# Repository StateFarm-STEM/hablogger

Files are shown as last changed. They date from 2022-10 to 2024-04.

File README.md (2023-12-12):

# High altitude Balloon (HAB) Logger

HABLogger is a project built to be usable by schools, community groups, youth organizations, and more as an introduction to programming, electronics and team building.

The [National Weather Service](https://www.weather.gov/chs/upperair) launches a minimum of two high altitude balloons a day from [91 locations](https://www.weather.gov/upperair/nws_upper) at 1100 and 2300 UTC to observe weather conditions used to model weather forecasts. When flying high altitude ballons, data is usually collected throughout the flight and later retrieved for analysis.

This project contains lessons wherein learners will launch their own weather balloon to the stratosphere, or approximately 90,000+ feet. Throughout the balloon flight, the components within the payload will collect temperature, barometric pressure, latitude, longitude, elevation, and other telemetry data. This information is collected via the peripheral modules attached to the microcontrollers within the payload and stored in an SD card for analysis after recovery.

The project contains basic hands-on experiences with the following:

- Microcontrollers & electronics, including wiring peripheral modules between a microcontroller and breadboard
- Programming microcontrollers to interact with peripheral modules using C programming language (Arduino microcontroller) or Python (Raspberry Pi Pico microcontroller)
- Launching a finished product in a high-altitude balloon flight to the stratosphere (90,000+ feet)
- Analyzing collected data after recovering the balloon payload

Each lesson is constructed to be completed within the timeframe of a typical classroom experience (approximately 45 minutes to 1 hour), and are designed to be completed by small groups (between 2 and 5 learners is recommended)

## Lesson Overview

- Lesson 1: Introduction and how to get started
  - Details about high altitude balloons
  - Introduction to electronics and components used in the project
  - Installing and using the preferred integrated development enviornment (IDE)
- Lesson 2: Blinking lights
  - Traditional first project with microcontrollers getting students comfortable with breadboards, components, microcontrollers, and loading code to the device 
- Lesson 3: Working with the weather sensor
  - Wiring up sensors to read temperature and barometric pressure
- Lesson 4: Working with the GPS module
  - Wiring up GPS hardware to the microcontroller and reading satellite telemetry
- Lesson 5: Working with the SD card module
  - Wire up SD card hardware then writing and reading contents from the SD card
- Lesson 6: Putting it all together
  - Wire everything up and write telemetry data to SD card
  - Read telemetry data from the SD card
- Analyzing telemetry and log data
  - Samples to interpret flight data

### Accessing the Lessons

The content is divided up by language and within the language you can choose the platform (where applicable).
- [C](https://github.com/StateFarm-STEM/hablogger/tree/main/c)
- [Python](https://github.com/StateFarm-STEM/hablogger/tree/main/python)

# Need Help?

- Report an issue by clicking the [issue](https://github.com/StateFarm-STEM/hablogger/issues) link towards the top of the page

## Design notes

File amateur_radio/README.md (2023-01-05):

# Amateur Radio In This Project

## Goals
To track the High Altitude Balloon, Amateur Radio is leveraged.  There are other tracking options that do not require a license, but among the goals are:
 - Introduce Amateur Radio to students and educators
 - Introduce new types of wireless communication with hands-on learning
 - Demonstrate the benefits of Amateur Radio beyond the balloon project, such as being able to communicate during emergencies
 - Show students there are Amateur Radio scholarships available, if they obtain their license.

## Overview
Amateur Radio, also known as Ham Radio, is the use of radio communications for the purposes of non-commercial exchange of messages, wireless experimentation, self-training, private recreation, and emergency communications.

Amateur Radio is utilized by the project to track and collect real-time flight telemetry information from the High Altitude Balloon, and locating the payload after landing.  HAB tracking via Amateur Radio is performed commonly via two means:
- Automatic Packet Reporting System (APRS)
- Weak Signal Propagation Reporter (WSPR) (pronounced whisper)

Each option has benefits and limitations, depending on the types of balloon and the tracking goals.

## Automatic Packet Reporting System (APRS)

APRS is a real time digital communication system that allows participants to share information, including position infromation, and other information about their locale that has 'immediate value' to all participants.

In its widest implementation, APRS communication occurs using VHF radios, with messages relayed to other stations, including repeaters on the ground, which can deliver the locale and telemetry infromation to APRS internet sites that allow users to view a map of APRS objects.

APRS works well for tracking goals of:
- High accuracy tracking is required (such as for payload retrival)
- Expected flight path is within local or regional area
- Expected flight path does NOT cross ocean or international waters
- Expected flight of balloon is rise to a max altitude and immediately return to earth
- Expected flight duration is a few hours or days

## Weak Signal Propagation Reporter (WSPR)

WSPR (prounced "whisper") is a protocol designed for weak-signal radio communication.  It is commonly used to by amateur radio operators for sending and recieving very low-power transmissions to test propagatino path on the Medium Frequency (MF) and High Frequency (HF) bands.  The protocol is designed and written initially by Joe Taylor (K1JT) and uses open source software developed and supported by  small team.  WSPR transmission, similiar to APRS, use a standard message format, carrying the station's call sign, Madienhead grid locator, and transmitter power in dBm.  The program decodes signals with a signal-to-noise (SNR) as low as -28 dB, with stations sending reports to online central database called WSPRnet, which includes mapping.

### References

[Weak Signal Propagation Reporter (WSPR)](https://en.wikipedia.org/wiki/WSPR_(amateur_radio_software))
[WSPR - Distant Whispers](http://www.g4ilo.com/wspr.html)
[WSPRNet](http://www.wsprnet.org/drupal/wsprnet/map)

## Tracking the balloon

## Getting your licensce

[Ham Radio School](https://www.hamradioschool.com/)

## Helpful links

[APRS.org](http://www.aprs.org/)

## Citation

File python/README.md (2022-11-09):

# HAB Logger
High Altitude Balloon Data Logging Project

Currently the Python version is supported on [Raspberry Pico hardware](https://www.raspberrypi.com/products/raspberry-pi-pico/). Your welcome to test on other RP2040 hardware platforms. If you do please let us know about your work by opening an [issue](https://github.com/StateFarm-STEM/hablogger/issues)!

Access the lessons [here](https://github.com/StateFarm-STEM/hablogger/tree/main/python/raspberrypico)

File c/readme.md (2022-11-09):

# C Language versions of the HAB Logger

Currently the HAB Logger is available and ready for use on [Arduino hardware](https://github.com/StateFarm-STEM/hablogger/tree/main/c/arduino). 

We are working on porting to the Raspberry Pico, we appreciate your patience!

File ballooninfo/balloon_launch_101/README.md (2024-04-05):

# How To Launch a High Altitude BAlloon (HAB) For Carrying The Project

## Overview

## Prediction Details

### Burst Calculations

[SondeHub Burst Calculation Website](https://sondehub.org/calc/)

- Modify the fields with a red star for your needs:
  - Payload Mass is the weight of everything below the balloon you will be flying in grams. A simple [Google search](https://www.google.com/search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) will yield the conversions
    - Rigging line(s), parachute, payload harness, Payload nd contents, and anything attached to the payload
  - Ballon Mass is the size balloon you will be flying. Be sure to select the proper size AND manufacturer. It's not a bad idea to validate the specs as we found the burst diameter a bit off.
  - Target Ascent rate in meters per second
    - For best camera results an ascent of 6 meters per second is optimal but you will likely need a different rate based on your lift gas volume
      - A flow gauge can be used to dial in the right amount of gas but they are typically cost prohibitive. These gauges are typically different for each type of gas as well.
    - You will need to modify this until the volume changes to your lift gas tank volume. A simple [Google search](https://www.google.com/search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) can convert m3 to cubic feet
   - Gas needs to be changed ot the lift gas you will be using. The calculations will be different for each lift gas option!

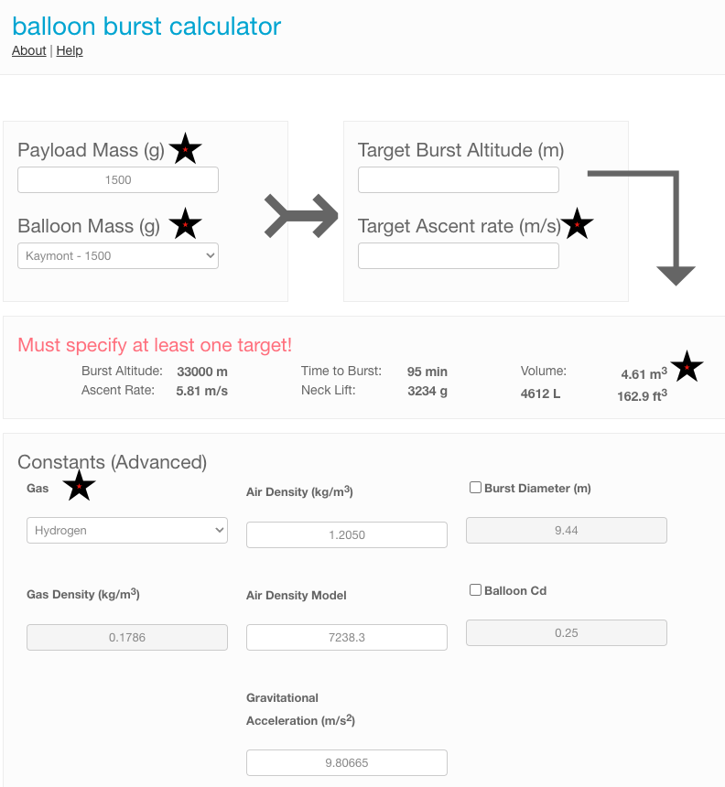
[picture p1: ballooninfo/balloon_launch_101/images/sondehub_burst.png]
SonceHub_Burst_image


## Landing Prediction Calculator

[Sonde HAB Prediction Calculator](https://predict.sondehub.org/)

- Modify the fields with a red star for your needs:
  - Latitude and Longitude
    - You can use many tools like [maps.google.com](maps.google.com)
      - Find the location best suited for winds at launch time and place a waypoint. The latitude and longitude will be shown or copied easily from the shared link
  - Launch Altitude
    - THis can be determined with many tools like Google Earth, USGS, [websites](https://whatismyelevation.com/), etc
      - Be sure to convert to meters
  - Launch time UTC
    - [Convert](https://www.google.com/search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) local time to UTC
- Launch Date
- Ascent Rate (m)
  - This was claculated fromt he above instructions on [SondeHub Burst Calculation Website](https://sondehub.org/calc/)
- Burst/Float Altitude (m)
  - This was claculated fromt he above instructions on [SondeHub Burst Calculation Website](https://sondehub.org/calc/)
- Descent Rate (m/s)
  - this will be defined by your parachute. Be sure you calculate based on the adjustments on your actual parachute as many can be reduced

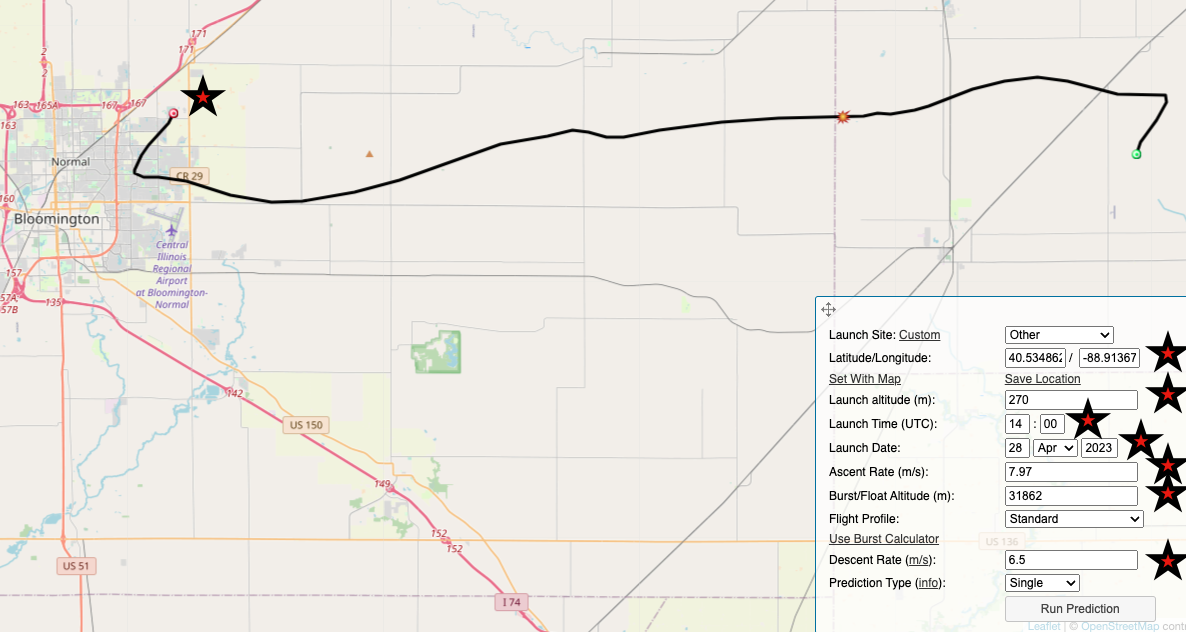
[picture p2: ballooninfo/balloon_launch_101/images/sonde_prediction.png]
SonceHub_Burst_image

-------

## Build payloads

### Pre-work / pre-launch

- Add camera mounts in the payload (top and sides)
- Mount external temp sensor and route wires to the logger
- Mount VHF antennas / dowell rods
  - Moxon
  - Di-pole
Ready the tracker(s)
- VHF APRS
- HF WSPR
- Other?
- Load batteries in the battery holders for the tracker
- Attach antennas to tracker(s) (HF and VHF)
Charge large battery packs
Data logger plugs into main battery pack

Ready Cameras
- Validate settings
- Ensure SD card is wiped
- Ensure they record a test video
  
Make rigging lines for filling and safety
- Two tethers for filling and moving to flight pad
- Rigging for payload attachment
- Release loop

Load everything needed for launch
- Battery
- Student data loggers(s)
- Tracker(s)
  - Battery pack(s)

Action Camera(s)
- Battery(s)
- SD card
Insta360
- Connect to battery(s) pack
- SD card(s)

Power splitter
If found contact note
Weather check / go no go
Prediciton calculation / go no go
Validate location of launch based on wind prediciton and / or other hazards
Contact local airport FAA / tower

### Day of launch

Weather check / go no go
Prediciton calculation / go no go
Setup filling station
- Stake tarp
- Unload tanks
- Ground tank
- Setup filler
  - Ground stake in the dirt
  - Ground wire attached to filler
- Setup rigging lines w caribeaners and attach:
  - To tank
  - To dumbell(s)
Undo balloon bag rubberbands

### Setup launch pads
Attach line to weight
Ensure team has their task list
Layout payload
- Layout payload downwind
- Kiteline to parachute
- Attach rigging line to parachute
- Rigging line to payload harness
- Attach 360 cam
- Attach rigging harness to payload

Power on battery pack(s)
Power on tracker
- Ensure pings are working on APRS and WSPR

Power on student data logger
Ensure all items are secure (duct tape where needed)
Setup cameras
- Plug into power
- Secure in camera holders
- Power insta360

Run prediction and share content / go no go
Monitor ADS-B for plane traffic
Fill balloon
Gloves on for anyone handling the balloons
Unroll balllon from UV bag
Attach neck to filler and tape
- Add 3 zips to balloon neck semi snug
- Attach zip - safety harness 1 to weight at filling station
- Attach zip - safety harness 2 to tank
- Attach payload rigging tether to zip
- Open gas and fill balloon semi slow
- Once tank is empty start sealing process
 - Move top zip up and seal tight
   - Clip excess
   - Tape sharp ends
 - Move second zip up and zip tight with safety harness to weight
 - Undo tape on filler nozzle and remove filler
 - Zip payload harness zip
   - Clip excess
   - Tape sharp ends
 - Tighten final zip
   - Clip excess
   - Tape sharp ends
 - Zip bottom of neck to above top zip
   - Clip excess
   - Tape sharp ends

Move ballon to launch location
- Balloon handler will bring their weight and harness to the fill location
- Clip launch pad weight to balloon
- Unclip fill weight harness
- Walk to launch location

Attach payload train to the payload harness
Confirm payload train is downwind and untangled with little slack
Fill next balloon(s) as directed above and move to launch pad(s)
Confirm tracker telemetry being recieved from balloon(s)
Confirm clear ADS-B for plane traffic
Unclip weights holding payload rigging

Countdown / release!
- Repeat other balloon(s)

## Laws and Regulations
- [Code of Federal Regulations - PART 101 - MOORED BALLOONS, KITES, AMATEUR ROCKETS, AND UNMANNED FREE BALLOONS](https://www.ecfr.gov/current/title-14/chapter-I/subchapter-F/part-101)
- [FAA Order JO 7110.65Z - Air Traffic Control](https://www.faa.gov/air_traffic/publications/atpubs/atc_html/chap9_section_6.html)

## Supplies

### Launch site protection and tools 
- Tarp (This is for protecting the balloon from sharp objects and loosing items in the grass / dirt)
- Stakes for the tarp 9Handy to hold the tarp down in the breeze / wind)
- Gloves for anyone touching the balloon (Nitrile or cotton if using hydrogen. These protect the latex from oils in handlers skin)
- Stocking caps (these will protect the balloon form oils in hair especially in windy conditions when the balloon bounces off of everything)
- Lift Gas (Choose lift gas thats available, most common since helium shortages is hydrogen)
- Gas regulator (this is specific by gas type)
- [Balloon filler](https://the-rocketman.com/weather-balloon-inflator-2/)
- Safety Weight (Used ot secure the balloon while filling as a secondary safety as well as when unclipping from the tank and moving to a launch location)
- Tether - Tank to balloon (Can be tied from paracord and use a clip for quick detachment)
- Tether - Balloon to safety weight (Can be tied from paracord and use a clip for quick detachment)
- Duct tape (Used for attaching payload items, sealing payload, other misc needs. use a high quality tape like gaffers tape or Gorilla brand etc)
- Electircal tape (Used to cover sharp edges when zip ties are clipped. Also used to seal balloon neck to the filler tube)
- [Heavy Zip ties](https://www.amazon.com/Industrial-250-lbs-Strength-Electrical-Karoka/dp/B099PF1LMM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) (Used for sealing the balloon - do not skimp on these, buy 250lb)
- Zip ties light (handy for tasks like attaching antenna wire, payload trinkets etc)
- Wire Flush Cutters (Used to trim zip ties as flush as possible as well as cut antenna wire)
- Adjustable wrench for regulator (Used to attach regualtor to the gas bottle)

### Balloon and payload
- [Ballon](https://www.kaymont.com/product-page/hab-tx-1500) (Consider using the TX balloons for cold conditions)
- [Parachute](https://the-rocketman.com/recovery-html/) (4' is typically sufficient)
- [Shock Cord - Open Loop (2 - 12')](https://the-rocketman.com/weather-balloon-y-harness-and-shock-cord/)
- [Payload harness - 4 way open loop ](https://the-rocketman.com/weather-balloon-y-harness-and-shock-cord/)
- Payload boxes (Styrofoam coolers work well)

### Payload contents
- [Light APRS / WSPR tracker](https://qrp-labs.com/lightaprsw2.html) (This allows real time tracking using amateur radio. Note this requires a licensced operator)
- Batteries for tracker (4 AAA work well, consider lithium cells)
- Battery holders for tracker (4 cell holders in serial)
- [Battery pack for cameras and student data loggers](https://www.amazon.com/gp/product/B09H4GLZXT/ref=ppx_yo_dt_b_search_asin_title?ie=UTF8&psc=1) (Any can be used jsut be sure to scale for your battery draw needs. These need to be inside the cooler or they will stop working at -10c)
- USB splitter cable (for powering cameras and data loggers)
- Cameras (action cameras similar to GoPro style cameras. Using generic brands will lesson the sting if the payload is lost. We have flown 4k 60fps units running about $140 each)

## [See seperate section on tracking](/amateur_radio/README.md)

## Helpful links

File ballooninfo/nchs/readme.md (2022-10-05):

# NCHS Launch 4-29-2022

- [Balloon Release](https://youtu.be/hP-R-rfDyBA)

- [Balloon Landing](https://youtu.be/S8HqcoTmZ1Y)

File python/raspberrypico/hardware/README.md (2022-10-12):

# Proposed hardware for the Raspberry Pico

## Listed below are proposed components for using Python on the Raspberry Pico
<br>
- I have added both micro SD card and a standard SD for size identification, these parts are small!
<br>
<br>

## BME-280 - Records temperature, humidity, and barametric pressure

- BME280 - Front
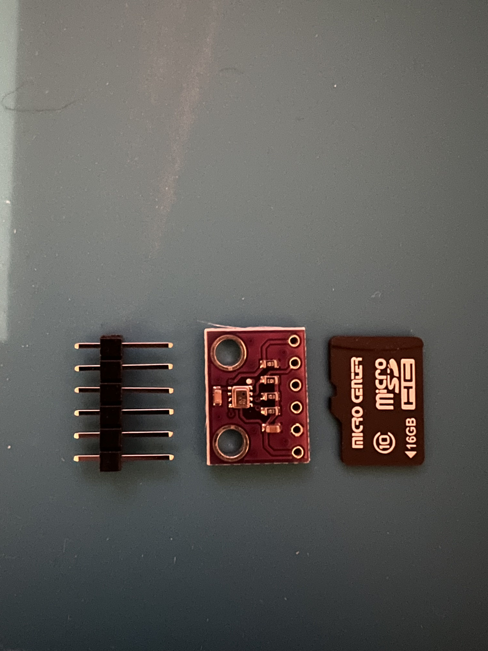
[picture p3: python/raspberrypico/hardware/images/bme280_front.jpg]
BME280 Front

- BME280 - Back
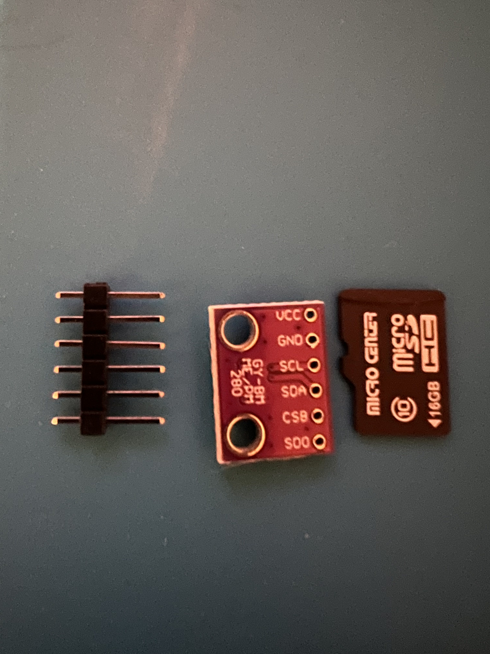
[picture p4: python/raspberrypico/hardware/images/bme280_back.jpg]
BME280 Back


## ESP32 Camera Module - Records pictures and videos, stores to SD, Wireless capabilities, and USB interface for programing and power

- ESP32 Camera Madule Camera Attached
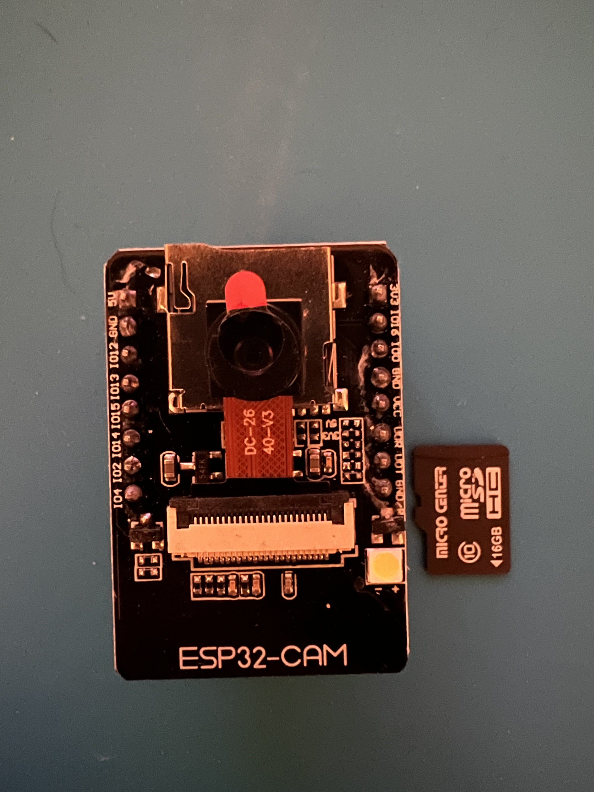
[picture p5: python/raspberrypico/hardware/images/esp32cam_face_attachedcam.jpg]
ESP32 Camera Madule Camera Attached

ESP32 Camera Madule Camera detached
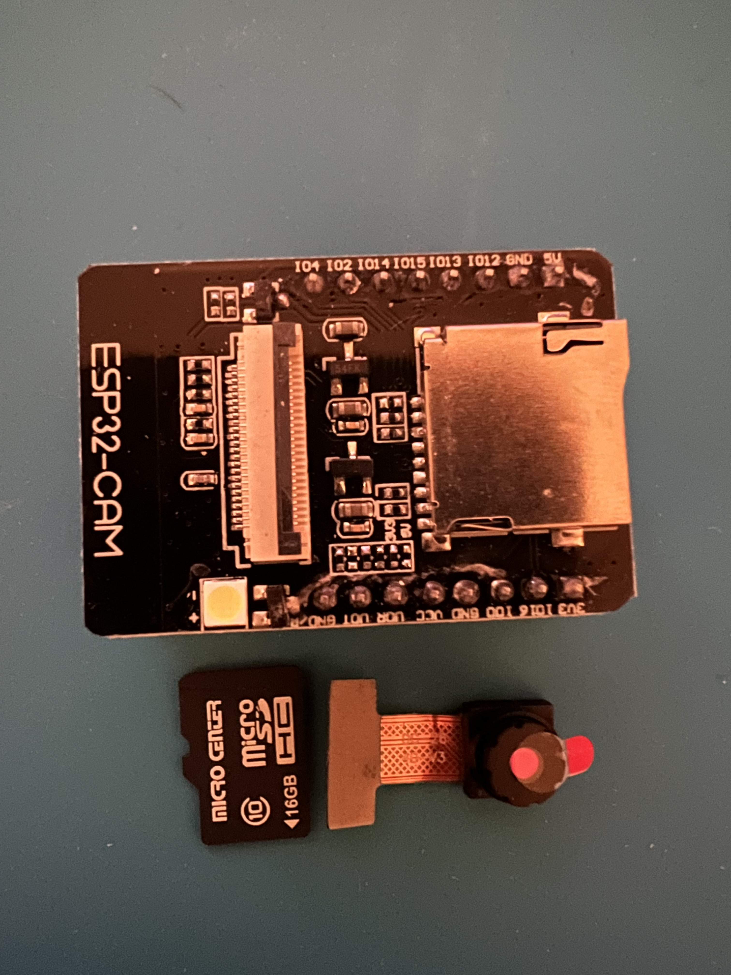
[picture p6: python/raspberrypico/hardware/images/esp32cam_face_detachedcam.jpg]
ESP32 Camera Madule Camera Detached

ESP32 Camera Madule Camera SD
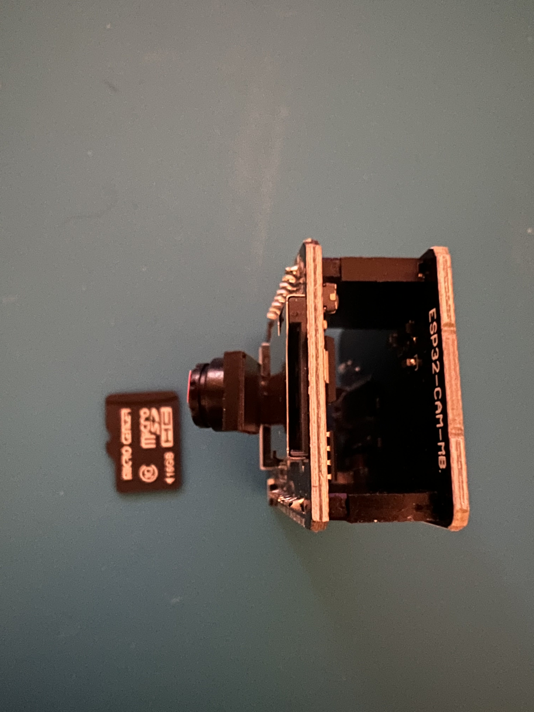
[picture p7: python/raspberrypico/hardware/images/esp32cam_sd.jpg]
ESP32 Camera Madule SD

ESP32 Camera Madule Camera USB Connector
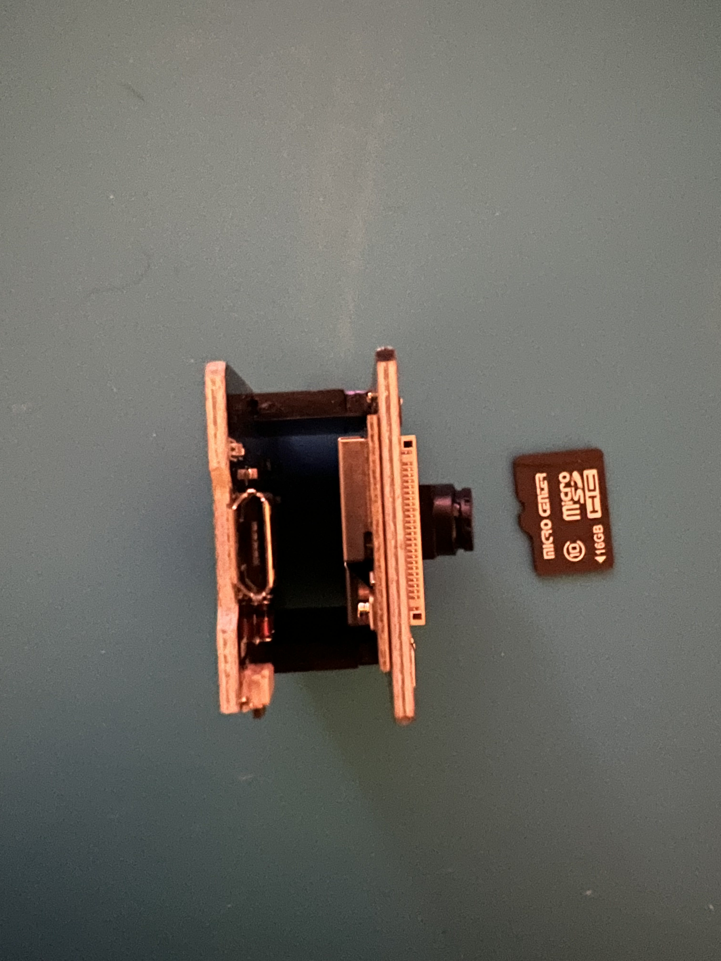
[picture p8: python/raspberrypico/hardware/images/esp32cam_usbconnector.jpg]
ESP32 Camera Madule USB Connector

ESP32 Camera Madule Camera Back
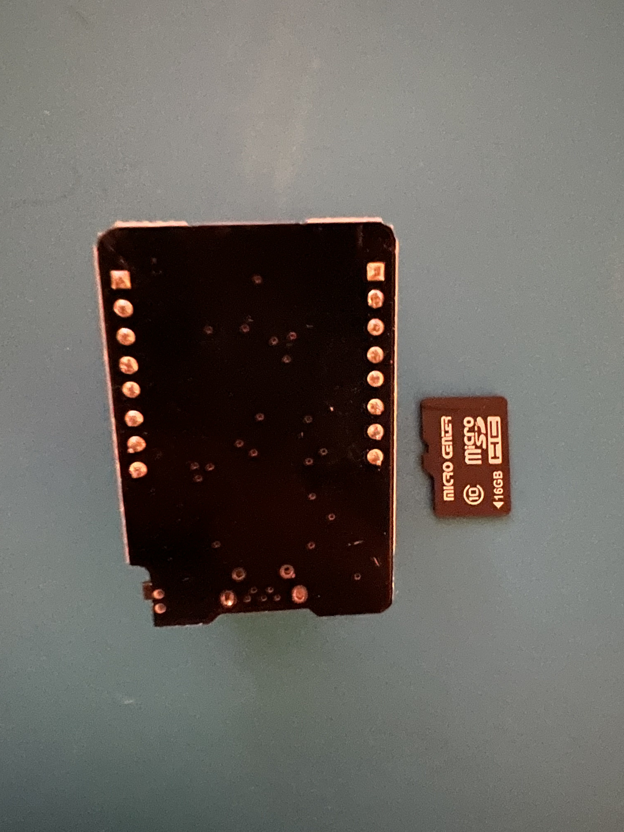
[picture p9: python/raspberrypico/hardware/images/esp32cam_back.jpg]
ESP32 Camera Madule Back


## [MPU-9250 - accelerometer, a gyroscope, and a magnetometer](https://components101.com/sensors/MPU9250-9-dof-mems-sensor-module-datasheet-pinout-features-working)

- MPU-9250 - Front
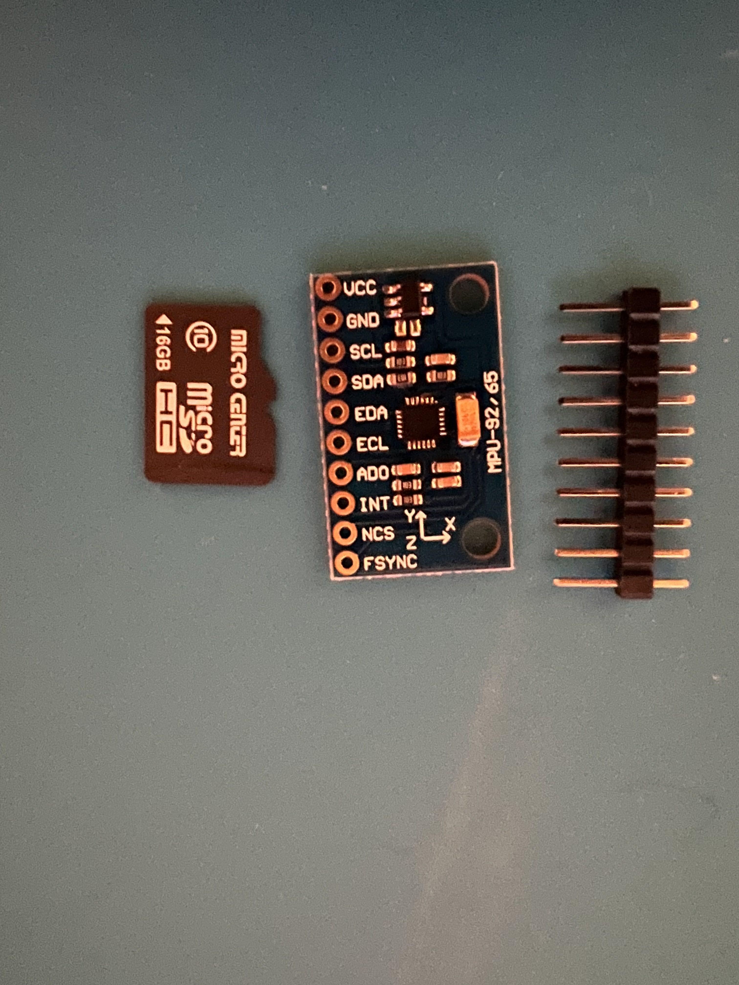
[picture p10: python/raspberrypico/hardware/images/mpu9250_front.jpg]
MPU-9250 - Front

- MPU-9250 - Back
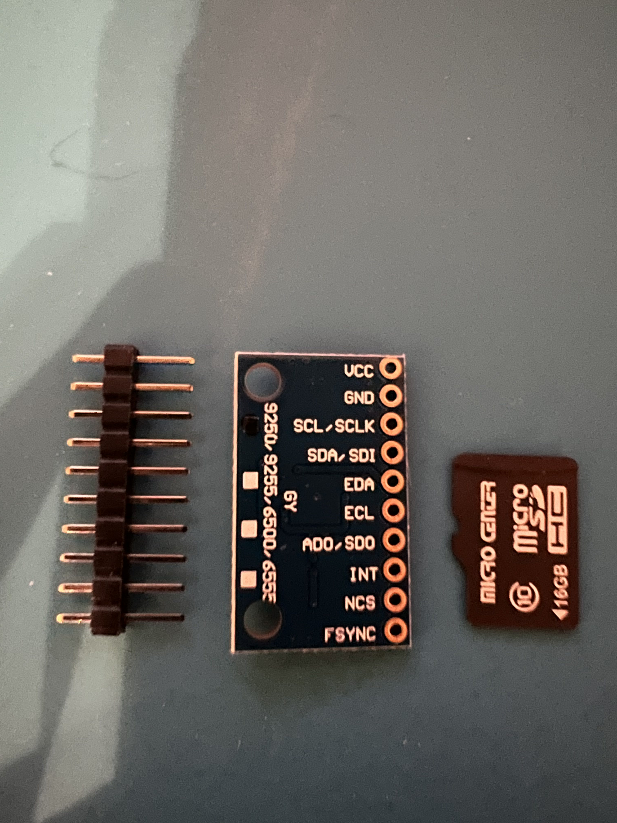
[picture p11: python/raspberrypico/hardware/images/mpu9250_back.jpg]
MPU-9250 - Back


## Raspberry Pico - Raspberry offering of a microcontroller

- All Raspberry Pico Offerings
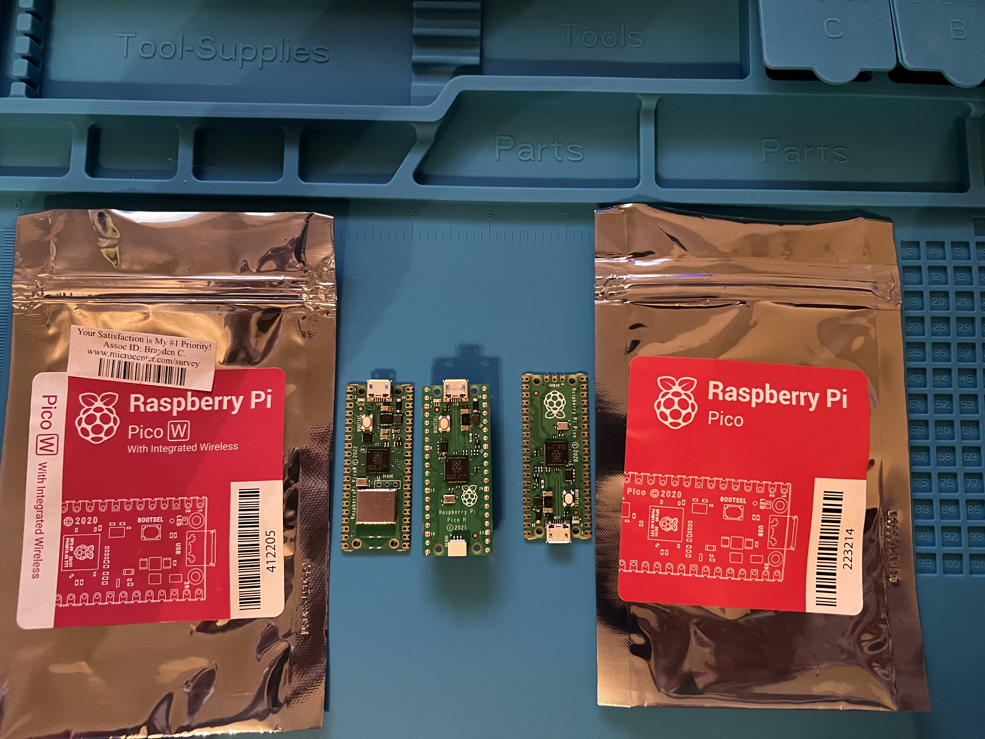
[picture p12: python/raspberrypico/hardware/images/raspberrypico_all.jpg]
All Raspberry Pico Offerings

- Raspberry Pico
Raspberry Pico - Front
Raspberry Pico - Back
- Raspberry Pico H - Headers
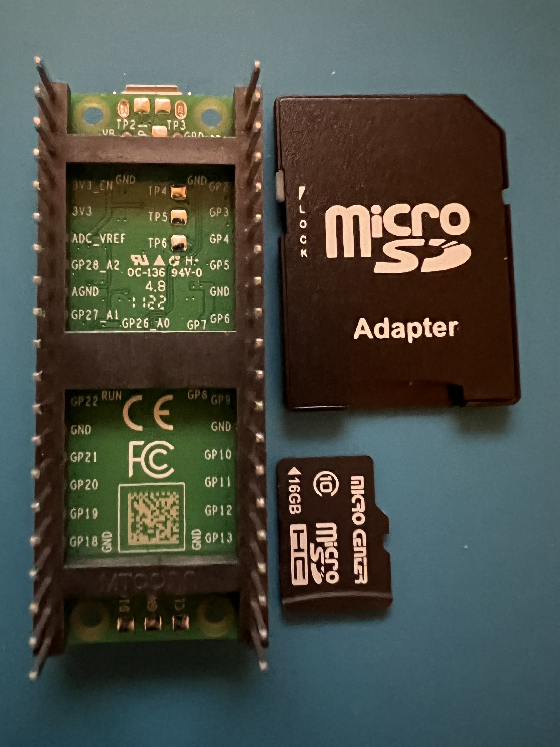
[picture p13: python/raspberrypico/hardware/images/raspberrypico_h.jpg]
Raspberry Pico - H

- Raspberry Pico H - Front
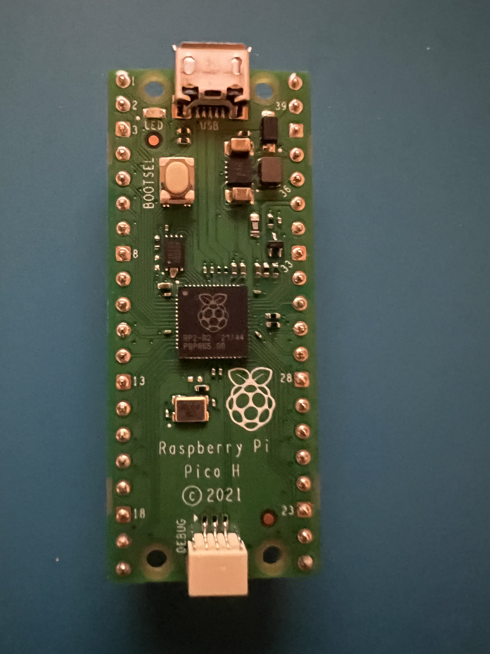
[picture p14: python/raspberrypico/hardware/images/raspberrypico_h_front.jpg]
Raspberry Pico - H Front

- Raspberry Pico W - Wireless
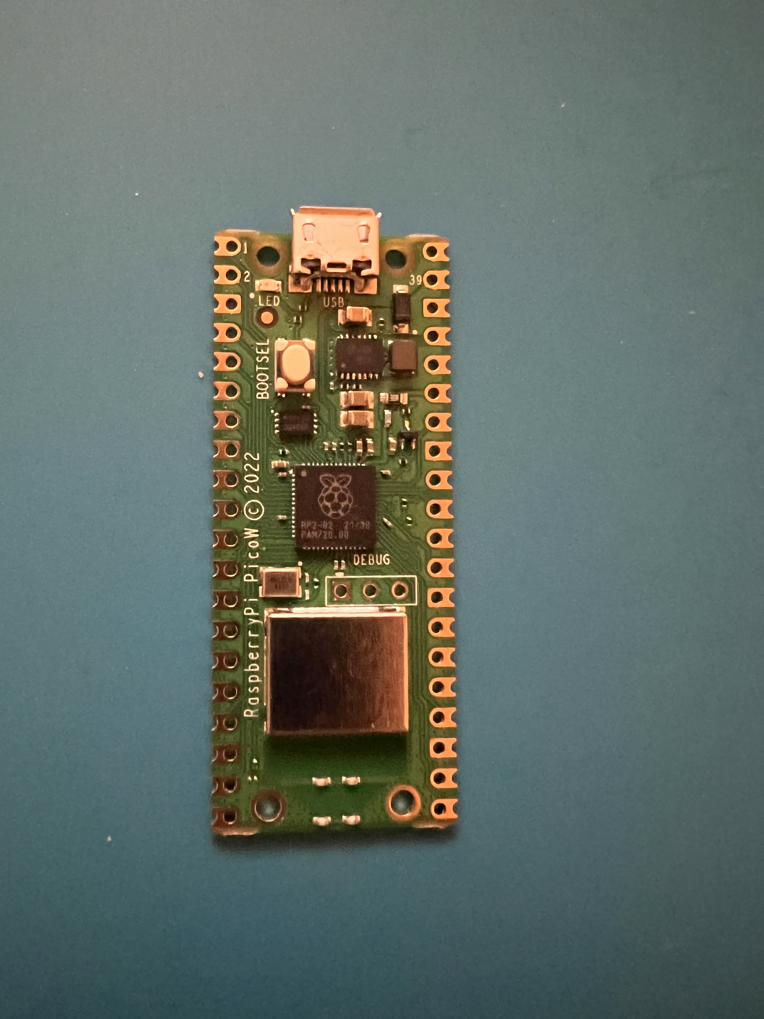
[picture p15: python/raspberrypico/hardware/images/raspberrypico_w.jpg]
Raspberry Pico - W - (Wireless)


## SD Reader - Enables SD card access to the microcontroller

- Front SD Card Reader
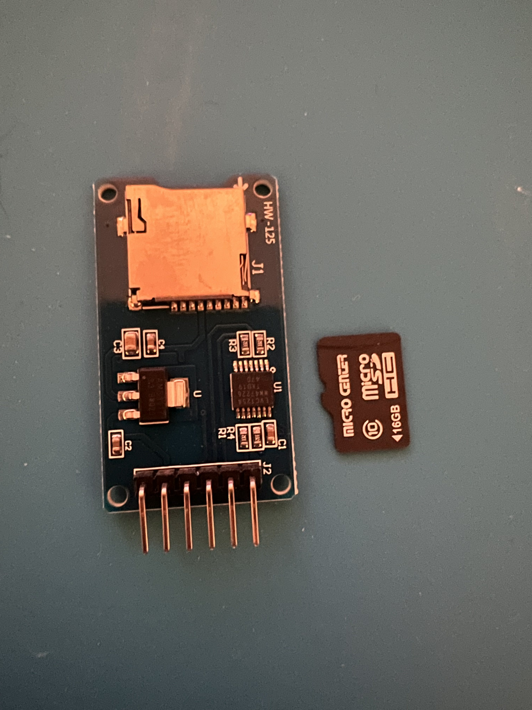
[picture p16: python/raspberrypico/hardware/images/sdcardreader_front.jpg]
SD Card Reader - Front

- Back SD Card Reader
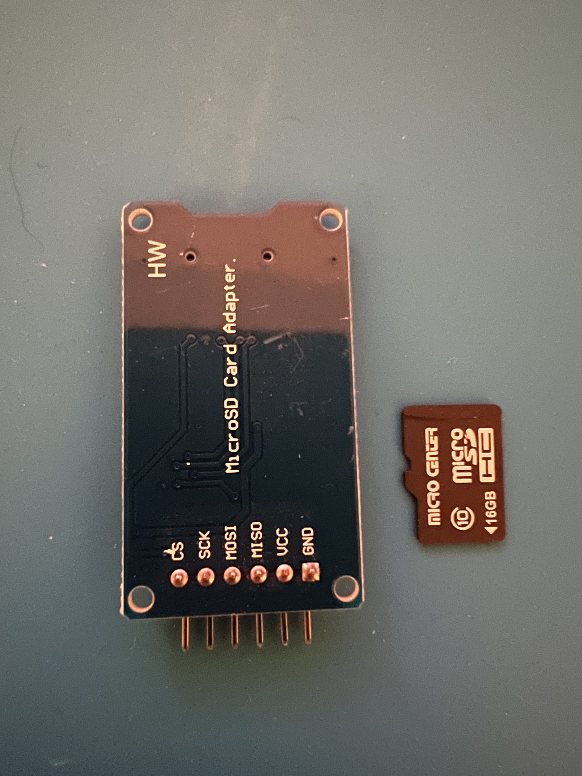
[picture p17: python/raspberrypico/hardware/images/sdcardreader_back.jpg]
SD Card Reader - Back


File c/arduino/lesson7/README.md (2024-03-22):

# Welcome to Lesson #7: oLED Display

## Present data to a display
<br>

#### Pre-requisites:
- It is recommended that you have successfully completed all the previous lessons 
<br><br>

#### Objectives:
- Breadboard the final circuit with an oLED
- Create a device that logs data such as pressure, altitude and temperature and displays onto a oLED display.
<br><br>

#### What you will be using:
- [Arduino IDE](/c/arduino/lesson4/screenshots/arduino-ide.png)
- [Arduino Uno](/c/arduino/lesson4/screenshots/arduino-uno-r3.png)

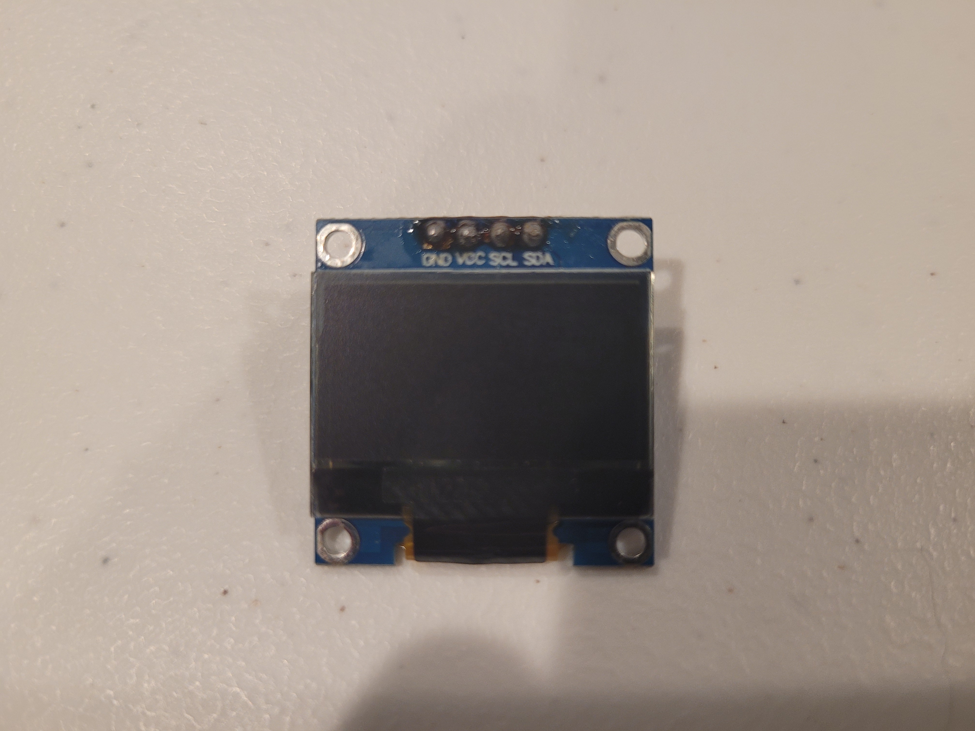
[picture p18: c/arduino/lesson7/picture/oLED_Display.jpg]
- 

- [BMP 180](/c/arduino/lesson1/photos/BMP_both.jpg)
- [GPS module](/c/arduino/lesson1/photos/GPS_NEO-6M.JPG)
- [Breadboard](/c/arduino/lesson6/screenshots/breadboard.png)
- [Wires](/c/arduino/lesson3/screenshots/1956-02.jpg)
<br><br>

#### What you will be learning:
- How to connect multiple different sensors or devices to the Arduino at the same time
  -  Breadboarding circuits
- How to write to an oLED display
- Connecting multiple [I2C](https://en.wikipedia.org/wiki/I%C2%B2C) modules
- Putting together all of the other lessons in order to make a final product
<br><br>

<!-- ### Video Walk-through
In addition to the reading below, you can watch this [video](videos/Lesson7.mp4?raw=true) for guidance!
<br><br> -->

## Wiring all the sensors and devices to the Arduino
<br>

- Remember you do not have to use the same color of jumper wire as this, but insure that your connections are the same. 
- In this lesson, we will be sharing the A4/A5 wires as the devices are I2C. Take note of the common wire up.
- **Unplug the Arduino from the computer while you are wiring it up**
<br><br>

#### Wiring the Arduino to the Breadboard
<br>

Module/Controller Pin | BB/Arduino Pins
----------- | ------------
**oLED Display**||
GND         | BB Ground (-)
VCC         | BB Power (+)
SCL         | Common SCL (Arduino A5)
SDA         | Common SDA (Arduino A4)
**GPS Sensor**||
VCC         | BB Power (+)
GND         | BB Ground (-)
PPS         | N/A
TXD         | 3
RXD         | 4
**Pressure Temperature Sensor**||
VIN         | BB Power (+)
GND         | BB Ground (-)
SCL         | Common SCL (Arduino A5)
SDA         | Common SDA (Arduino A4)
**Arduino**||
5V          | BB Power (+)
GND         | BB Ground (-)

## Full wire up
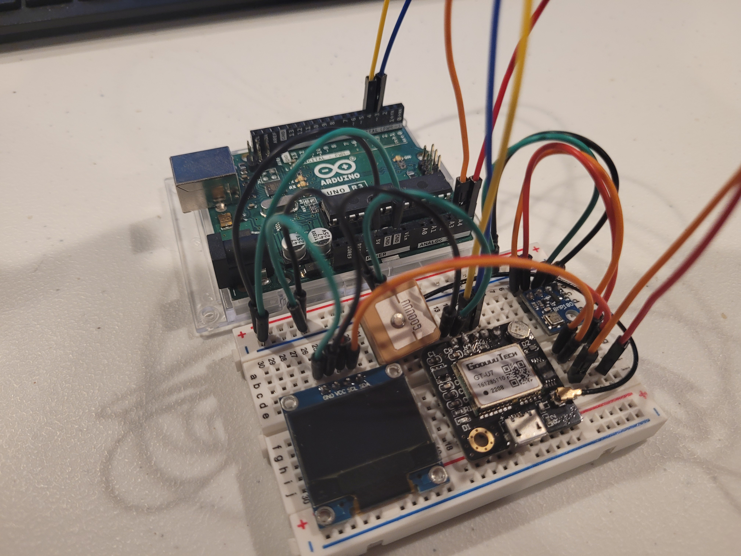
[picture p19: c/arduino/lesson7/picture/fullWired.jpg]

<br><br>

## Common SCL/SDA
The BMP180 and oLED Display will share the SCL/SDA A5/A4 spot on the Arduino. [I2C](https://en.wikipedia.org/wiki/I%C2%B2C) addresses are used to differentiate between the two modules.
<br>
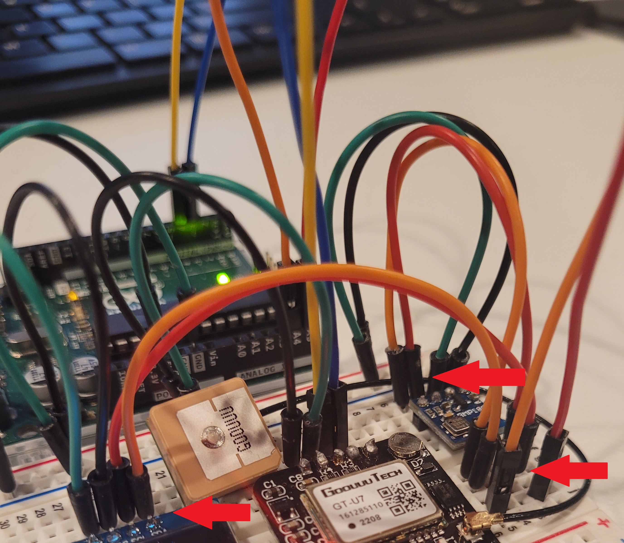
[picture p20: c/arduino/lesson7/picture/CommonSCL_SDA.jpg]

<br><br>

### Validate Libraries
Make sure that all the libraries below are installed in the IDE. Without these libraries the code below will not function and will error out.
* Adafruit bmp085 library
* BusIO
* TinyGPSPlus

***NOTE***: A new library is needed for this build. Install ```Adafruit SSD1306``` library through the Arduino IDE by going to Sketch -> Include Library -> Manage Libraries -> then search for ```Adafruit SSD1306```. Install the depending ```Adafruit GFX``` library as well.
<br><br>

<details>

<summary>Working Code - Copy and paste this into your sketch </summary>

```java
#include <SPI.h>
#include "Adafruit_BMP085.h"
#include <TinyGPSPlus.h>
#include <SoftwareSerial.h>

#include <Adafruit_GFX.h>
#include <Adafruit_SSD1306.h>

#define SCREEN_WIDTH 128 // OLED display width, in pixels
#define SCREEN_HEIGHT 64 // OLED display height, in pixels

// Declaration for an SSD1306 display connected to I2C (SDA, SCL pins)
// The pins for I2C are defined by the Wire-library. 
// On an arduino UNO:       A4(SDA), A5(SCL)
// On an arduino MEGA 2560: 20(SDA), 21(SCL)
// On an arduino LEONARDO:   2(SDA),  3(SCL), ...
#define OLED_RESET     -1 // Reset pin # (or -1 if sharing Arduino reset pin)
#define SCREEN_ADDRESS 0x3C ///< See datasheet for Address; 0x3D for 128x64, 0x3C for 128x32
Adafruit_SSD1306 display(SCREEN_WIDTH, SCREEN_HEIGHT, &Wire, OLED_RESET);

const int chipSelect = 10;
const bool bypassGPS = true;

static const int RXPin = 4, TXPin = 3;
static const uint32_t GPSBaud = 9600;
TinyGPSPlus gps;

// map software serial to gps
SoftwareSerial serialgps(TXPin, RXPin);

Adafruit_BMP085 bmp;

void setup() {
  // SSD1306_SWITCHCAPVCC = generate display voltage from 3.3V internally
  if(!display.begin(SSD1306_SWITCHCAPVCC, SCREEN_ADDRESS)) {
    //Serial.println(F("SSD1306 allocation failed"));
    for(;;); // Don't proceed, loop forever
  }

  // Show initial display buffer contents on the screen --
  // the library initializes this with an Adafruit splash screen.
  display.display();

  bmp.begin();

  serialgps.begin(GPSBaud);
  delay(2000);
  if (!serialgps.available()) {
    //Serial.println(F("initialization failed"));
    for(;;);
  }
}

void loop() {
  
  // make a string for assembling the data to log:
  String dataString = "";
  bool gpsready = false;

  float lat = 0;
  float lng = 0;

  unsigned long start = millis();
  do
  {
    while (serialgps.available()>0) {
      char c;
      c=serialgps.read();
      gps.encode(c);
    }
  } while (millis() - start < 5000);

  float c = bmp.readTemperature();  // Variable for holding temp in C
  float f = c*1.8 + 32.;  // Variable for holding temp in F
  //float pressure = bmp.readPressure()/3386.3887; //pascals to in of mercury
  float p = bmp.readPressure(); //pascals
  
  if ((gps.location.age() < 1000 || gps.location.isUpdated()) && gps.location.isValid()) {
    if (gps.satellites.isValid() && (gps.satellites.value() >= 3)) {
      lat = gps.location.isValid() ? gps.location.lat() : 0;
      lng = gps.location.isValid() ? gps.location.lng() : 0;

      gpsready = true;
    }
  }

  if (gpsready || bypassGPS) {   

      // Clear the buffer
      display.clearDisplay();

      display.setTextSize(1);             // Normal 1:1 pixel scale
      display.setTextColor(SSD1306_WHITE);        // Draw white text
      display.setCursor(0,0);             // Start at top-left corner
      display.print(F("Temperature: "));
      display.print(f);
      display.print(F(" F"));

      display.setTextSize(1);             // Normal 1:1 pixel scale
      display.setTextColor(SSD1306_WHITE);        // Draw white text
      display.setCursor(0,9);             // Start at top-left corner
      display.print(F("Pressure: "));
      display.print(p);

      display.setTextSize(1);             // Normal 1:1 pixel scale
      display.setTextColor(SSD1306_WHITE);        // Draw white text
      display.setCursor(0,18);             // Start at top-left corner
      display.print(F("Lat: "));
      display.print(String(lat, 6));

      display.setTextSize(1);             // Normal 1:1 pixel scale
      display.setTextColor(SSD1306_WHITE);        // Draw white text
      display.setCursor(0,27);             // Start at top-left corner
      display.print(F("Lng: "));
      display.print(String(lng, 6));

      display.setTextSize(1);             // Normal 1:1 pixel scale
      display.setTextColor(SSD1306_WHITE);        // Draw white text
      display.setCursor(0,36);             // Start at top-left corner
      display.print(F("Altidtude: "));
      display.print(String((long)gps.altitude.feet(), 6));

      display.setTextSize(1);             // Normal 1:1 pixel scale
      display.setTextColor(SSD1306_WHITE);        // Draw white text
      display.setCursor(0,45);             // Start at top-left corner
      display.print(F("Satellites: "));
      display.print(String((int)gps.satellites.value()));

      // Show the display buffer on the screen. You MUST call display() after
      // drawing commands to make them visible on screen!
      display.display();    
  }

  delay(2000);
}
```
</details>
<br>

## Want more?
If you have finished with the base lesson, check out the items below.
<br><br>

Things to think about, validate, and/or try:
* Is the data being written out correct? 🤔
* What are some things you could do to test all the modules at once?
* Change the order/format of the output display data to your liking.
* Load the demo display code to see the full power of the oLED! 😵 (File > Adafruit SSD1306 > ssd1306_128x64_i2c) <br>
(***HINT:*** Change the ```SCREEN_ADDRESS``` to ```0x3C```)

## Challenge  
If you have finished with the extension lesson questions, check out the challenge below.
<br><br>

Create you own custom image, load it into a byte array, and display your image on the the oLED. [External walkthrough here!](https://www.instructables.com/How-to-Display-Images-on-OLED-Using-Arduino/) 🐧 Make sure that the image is appropriate in both size, scale, color...and taste. 😅
<br><br>

<details>

<summary>Try to write the code on your own. If you get stuck or need some inspiration expand this section.</summary>

```java
#include <SPI.h>
#include <Wire.h>
#include <Adafruit_GFX.h>
#include <Adafruit_SSD1306.h>

#define SCREEN_WIDTH 128 // OLED display width, in pixels
#define SCREEN_HEIGHT 64 // OLED display height, in pixels

// Declaration for an SSD1306 display connected to I2C (SDA, SCL pins)
// The pins for I2C are defined by the Wire-library. 
// On an arduino UNO:       A4(SDA), A5(SCL)
// On an arduino MEGA 2560: 20(SDA), 21(SCL)
// On an arduino LEONARDO:   2(SDA),  3(SCL), ...
#define OLED_RESET     -1 // Reset pin # (or -1 if sharing Arduino reset pin)
#define SCREEN_ADDRESS 0x3C ///< See datasheet for Address; 0x3D for 128x64, 0x3C for 128x32
Adafruit_SSD1306 display(SCREEN_WIDTH, SCREEN_HEIGHT, &Wire, OLED_RESET);

#define LOGO_HEIGHT   16
#define LOGO_WIDTH    16

// 'RickAndMorty', 128x64px
const unsigned char epd_bitmap_RickAndMorty [] PROGMEM = {
  0x00, 0x00, 0x00, 0x00, 0x00, 0x00, 0x00, 0x00, 0x00, 0x00, 0x00, 0x00, 0x00, 0x00, 0x00, 0x00, 
  0x00, 0x00, 0x00, 0x00, 0x00, 0x00, 0x00, 0x00, 0x00, 0x00, 0x00, 0x00, 0x00, 0x00, 0x00, 0x00, 
  0x00, 0x00, 0x00, 0x00, 0x00, 0x00, 0x00, 0x00, 0x00, 0x00, 0x00, 0x00, 0x00, 0x00, 0x00, 0x00, 
  0x00, 0x00, 0x00, 0x00, 0x00, 0x00, 0x00, 0x00, 0x00, 0x00, 0x03, 0x00, 0x00, 0x00, 0x00, 0x00, 
  0x00, 0x00, 0x00, 0x00, 0x00, 0x00, 0x00, 0x00, 0x00, 0x00, 0x05, 0x00, 0x00, 0x00, 0x00, 0x00, 
  0x00, 0x70, 0x00, 0x00, 0x00, 0x00, 0x00, 0x00, 0x00, 0x00, 0x05, 0x00, 0x00, 0x00, 0x00, 0x00, 
  0x01, 0x88, 0x00, 0x00, 0x00, 0x00, 0x00, 0x00, 0x00, 0x00, 0x09, 0x00, 0x00, 0x00, 0x00, 0x00, 
  0x07, 0x06, 0x00, 0x00, 0x00, 0x00, 0x00, 0x00, 0x00, 0x00, 0x0d, 0x00, 0x00, 0x00, 0x00, 0x00, 
  0x10, 0x00, 0x80, 0x00, 0x00, 0x00, 0x00, 0x00, 0x00, 0x0a, 0x0a, 0x00, 0x00, 0x00, 0x00, 0x00, 
  0x20, 0x00, 0xc0, 0x00, 0x00, 0x00, 0x00, 0x00, 0x00, 0x0a, 0x12, 0x00, 0x00, 0x00, 0x00, 0x00, 
  0x40, 0x00, 0x20, 0x00, 0x00, 0x00, 0x00, 0x00, 0x00, 0x12, 0x12, 0x00, 0x00, 0x00, 0x00, 0x00, 
  0x40, 0x00, 0x20, 0x00, 0x00, 0x00, 0x00, 0x00, 0x00, 0x12, 0x32, 0x00, 0x00, 0x00, 0x00, 0x00, 
  0x40, 0x00, 0x20, 0x00, 0x00, 0x00, 0x00, 0x00, 0x00, 0x34, 0x22, 0x00, 0x00, 0x00, 0x00, 0x00, 
  0x20, 0xf0, 0x23, 0x00, 0x00, 0x00, 0x00, 0x00, 0x00, 0x6c, 0x22, 0x00, 0x00, 0x00, 0x00, 0x00, 
  0x23, 0x9c, 0x00, 0x80, 0x04, 0x00, 0x00, 0x00, 0x00, 0x8e, 0x22, 0x00, 0x00, 0x00, 0x00, 0x00, 
  0x23, 0x0c, 0x14, 0x80, 0x0a, 0x00, 0x00, 0x00, 0x00, 0x82, 0x42, 0x00, 0x00, 0x10, 0x00, 0x00, 
  0x21, 0x04, 0x14, 0x80, 0x12, 0x00, 0x00, 0x00, 0x00, 0x82, 0x42, 0x00, 0x00, 0x20, 0x00, 0x00, 
  0x21, 0x06, 0x14, 0x80, 0x12, 0x00, 0x00, 0x00, 0x01, 0x02, 0x42, 0x00, 0x00, 0x48, 0x00, 0x00, 
  0x21, 0x02, 0x04, 0x80, 0x12, 0x0c, 0x00, 0x00, 0x01, 0x02, 0x42, 0x00, 0x00, 0x50, 0x00, 0x00, 
  0x12, 0x02, 0x04, 0x80, 0x12, 0x18, 0x00, 0x00, 0x01, 0x23, 0xc3, 0x00, 0x00, 0xd0, 0x00, 0x00, 
  0x10, 0x86, 0x23, 0x80, 0x12, 0x24, 0x00, 0x00, 0x01, 0x23, 0x81, 0x00, 0x7c, 0x90, 0x00, 0x00, 
  0x10, 0x84, 0x23, 0x80, 0x13, 0x74, 0x00, 0x00, 0x01, 0x21, 0x01, 0x09, 0x62, 0x80, 0x00, 0x00, 
  0x10, 0x84, 0x20, 0x87, 0xf3, 0xc8, 0x00, 0x01, 0x02, 0x21, 0x31, 0x1f, 0x43, 0xb1, 0x40, 0x00, 
  0x10, 0x8c, 0xc4, 0x88, 0x33, 0x10, 0x18, 0x05, 0x02, 0x31, 0x3d, 0x23, 0x03, 0xd1, 0x40, 0x00, 
  0x10, 0x58, 0x44, 0xda, 0x62, 0x30, 0x28, 0x05, 0x02, 0x31, 0x39, 0xc1, 0x21, 0x91, 0x20, 0x00, 
  0x00, 0x70, 0x44, 0xe1, 0xe0, 0x20, 0x2c, 0x3d, 0x02, 0x3d, 0x19, 0xc1, 0x11, 0x11, 0x20, 0x00, 
  0x00, 0x20, 0x84, 0xe1, 0xe0, 0x20, 0x67, 0xdd, 0x02, 0x39, 0x10, 0x81, 0x31, 0x3b, 0x20, 0x00, 
  0x08, 0x01, 0x04, 0xf2, 0x20, 0xc0, 0x44, 0xd9, 0x02, 0x39, 0x10, 0xd1, 0x11, 0x3f, 0x20, 0x00, 
  0x08, 0x03, 0x04, 0xe6, 0x21, 0x80, 0x74, 0xd9, 0x02, 0x29, 0x30, 0x11, 0x01, 0x07, 0x30, 0x00, 
  0x08, 0x03, 0x04, 0x4c, 0x31, 0x80, 0x14, 0x19, 0x02, 0x2c, 0x30, 0x3d, 0x0e, 0x01, 0x10, 0x00, 
  0x04, 0x01, 0x04, 0x44, 0x30, 0x80, 0xcc, 0x11, 0x02, 0x24, 0x30, 0x31, 0x8f, 0x21, 0x30, 0x00, 
  0x04, 0x00, 0xc6, 0x44, 0x30, 0xc0, 0xc4, 0x01, 0x02, 0x24, 0x30, 0x30, 0x07, 0x3d, 0x00, 0x00, 
  0x04, 0x40, 0xe0, 0x0f, 0xf0, 0x40, 0x80, 0x01, 0x04, 0x44, 0x39, 0x98, 0x07, 0x3f, 0x08, 0x1c, 
  0x04, 0x70, 0x22, 0x48, 0xb2, 0x20, 0x90, 0x09, 0x04, 0x44, 0xf1, 0x00, 0x27, 0x21, 0x08, 0x24, 
  0x04, 0x78, 0x12, 0x40, 0x36, 0x50, 0xb0, 0x81, 0x04, 0x46, 0x49, 0x01, 0x23, 0x21, 0x08, 0x4c, 
  0x04, 0xce, 0x1a, 0xc0, 0x7f, 0x10, 0x30, 0x91, 0x04, 0x42, 0x48, 0x81, 0x33, 0x20, 0x8d, 0x88, 
  0x04, 0x03, 0x0e, 0xe1, 0xf7, 0x10, 0xbb, 0xe4, 0x04, 0x42, 0x48, 0xe3, 0x33, 0x20, 0xcf, 0x10, 
  0x04, 0x01, 0x0e, 0xe7, 0x25, 0x00, 0xaa, 0x3c, 0x04, 0x81, 0x4c, 0xff, 0x3b, 0x20, 0x84, 0x20, 
  0x04, 0x40, 0xc6, 0x96, 0x24, 0x88, 0x00, 0x07, 0x04, 0x81, 0x84, 0x80, 0xcb, 0x20, 0x80, 0xc0, 
  0x04, 0x40, 0x62, 0x94, 0x28, 0x88, 0x00, 0x00, 0x04, 0x80, 0x04, 0x80, 0x0b, 0x00, 0x83, 0x80, 
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
};

void setup() {
  Serial.begin(9600);

  // SSD1306_SWITCHCAPVCC = generate display voltage from 3.3V internally
  if(!display.begin(SSD1306_SWITCHCAPVCC, SCREEN_ADDRESS)) {
    Serial.println(F("SSD1306 allocation failed"));
    for(;;); // Don't proceed, loop forever
  }

  // Show initial display buffer contents on the screen --
  // the library initializes this with an Adafruit splash screen.
  //display.display();
  //delay(2000); // Pause for 2 seconds

  // Clear the buffer
  display.clearDisplay();

  display.drawBitmap(0, 0, epd_bitmap_RickAndMorty, 128, 64, WHITE);
  display.display();
}

void loop() {
}
```

</details>

### Review
- Learned how to connect multiple different sensors or devices to the Arduino at the same time
  -  Breadboarding circuits
- How to display to an oLED Display
- Put all of the other lessons together in order to make a final product
<br><br>

### Trouble shooting
- Unplug/reset the Arduino and check all of the connections and try running it again
- GPS not reading coordinates is likely caused by obstruction of the signal so moving  outside may be necessary
- Validate that all libraries are installed for use (BMP180 and GPS)
- No display change? GPS never initialized and code is stuck. Validate GPS is setup correctly.
<br><br>

<!-- ### Need help?
Watch the walk-through [video](videos/Lesson6.mp4?raw=true) for guidance! -->

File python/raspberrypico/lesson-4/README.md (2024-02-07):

# Lesson 4: GPS Coordinates

## High Altitude Balloon Data Logging

### Pre-requisites
* Complete [Lesson 1: Blinking Light](../lesson1/README.md)
* [Thonny Python IDE](https://thonny.org/) installed on your computer
* All necessary hardware components (Raspberry Pi Pico, GTU-7 module, breadboard, wires, USB cable, computer)

### Objectives
* Use breadboard to wire GTU-7 module to Raspberry Pi Pico
* Install the GTU-7 MicroPython driver to the Raspberry Pi Pico
* Print GPS coordinates to the console

### Results
* Familiarity with wiring a breadboard
* Understanding of basic MicroPython code
* Learn the importance of MicroPython drivers and how to use them
* A functioning program for reading GPS data and printing the information to the console<br><br>

### Video Walk-through
In addition to the reading below, you can watch this [video](./docs/videos/Lesson4.mp4?raw=true) for guidance!
<br><br>

## Steps

  **IMPORTANT** Before wiring your Pico, UNPLUG IT FROM YOUR COMPUTER. If plugged in while wiring, you risk damaging the Pico or GT-U7 module.

1. Wire the GT-U7 to the Raspberry Pi Pico.
    GT-U7 Pins | Description | Pi Pico Pins
    ------------ | ----------- | ------------
    VCC          | (Voltage In): Provides power. Connect to the 5V pin on Pico | 5V (40)
    GND          | (Ground): Connect to the ground pin on Pico | GND (38)
    PPS          | (Pulse Per Second): Assists with synchronization | N/A
    TXD          | (Transmit): Transmission pin used for serial communication | UART1 RX / GP5 (7)
    RXD          | (Receive): Receiver pin used for serial communication | UART1 TX / GP4 (6)

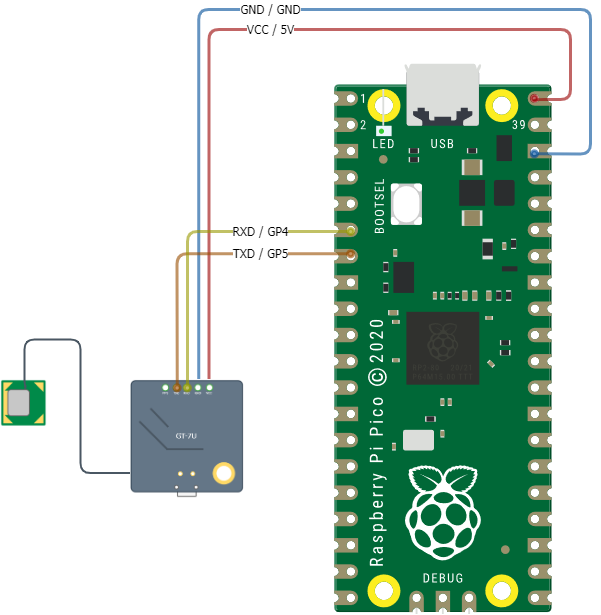
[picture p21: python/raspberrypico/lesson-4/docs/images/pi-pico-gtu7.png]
gtu7-diagram
    

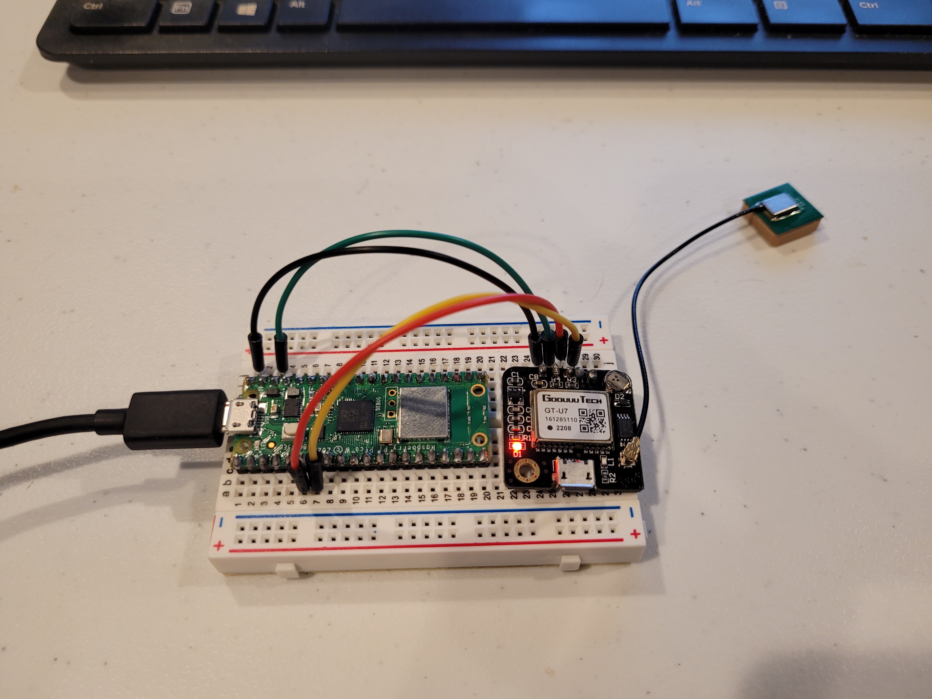
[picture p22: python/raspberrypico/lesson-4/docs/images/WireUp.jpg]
Lesson Four
    

### Install GT-U7 Driver

Drivers are code modules for enabling certain functionality. One such driver allows us to read data from the GTU-7 module. This driver is called `gtu7.py` and is located in the [../drivers/src/gtu7.py](../drivers/src/gtu7.py) location. The following steps will result in saving this driver to the Raspberry Pi Pico so the driver can be used by our Python code.

1. Download the driver called `gtu7.py` located in the [../drivers/src/gtu7.py](../drivers/src/gtu7.py) location to a directory/file/location of your choice. Remember where you downloaded the driver to for a later step.

1. Connect your Raspberry Pi Pico to your computer using the USB cable.

1. Open the Thonny IDE. _Stop/Restart_ the backend to refresh the connection.

    stop-restart

    You should now see `Raspberry Pi Pico` displayed in the left-hand navigation of Thonny.If the "Files" window is not displaying add it from the View > Files menu.

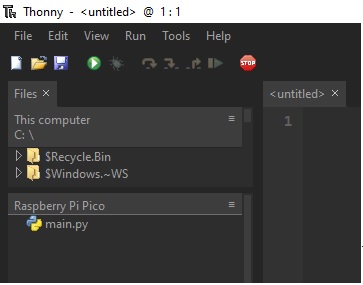
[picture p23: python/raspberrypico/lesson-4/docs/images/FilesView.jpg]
files-menu
    

1. If one does not already exist, create a new directory in Thonny on the Raspberry Pi Pic called `drivers`.
    
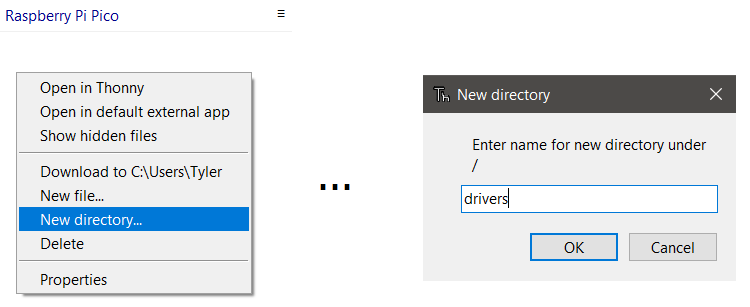
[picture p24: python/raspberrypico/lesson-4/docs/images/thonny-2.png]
drivers-directory
    

1. Using Thonny, select _File_ then _Open_ from the menu. Choose _This Computer_. Navigate to the location where you downloaded `gtu7.py` in step 1. Select the file and click _Open_.

1. Save the `gtu7.py` file to the Raspberry Pi Pico. This allows our code to use the driver to perform GT-U7 actions in MicroPython when running on the Pi Pico. 

    Click _File_ then _Save as..._. Choose _Raspberry Pi Pico_. Double-click the `drivers` folder created in a previous step. Then save the `gtu7.py` file being sure to name it `gtu7.py`.

1. If a file called `__init__.py` does not already exist in the `/drivers` folder, create a new file in Thonny called `__init__.py`. 

    Click _File_ then _New_. Then click _File_ then _Save as..._. Choose _Raspberry Pi Pico_ and save this empty file to the same `drivers` location as the previous step. Name the file `__init__.py`. This empty file is used by Python to indicate the `drivers` folder is to be used for Python modules.

    Your finished folders and files should look like this:<br>
    files-menu

### GT-U7 Program

The steps in this section will use the previous hardware and driver sections to allow reading temperature, pressure, and altitude from the GT-U7 module. The code example for this lesson is located in [./src/main.py](./src/main.py).

1. Using Thonny, open the `main.py` file in [./src/main.py](./src/main.py).

1. Run the script.

    run-script

    Output will be generated to the console in Thonny describing the actions being taken. You will see output for latitude, longitude, number of satellites, and time returned from the GPS module.

    Example output:

    ```
    Latitude: 	 4026.774
    Longitude: 	 -8902.08
    Satellites:  6
    Time:		 18:46:14
    ```

#### Is Your GPS Module Not Connecting?

In some locations, such as the center of a building or in a basement, the GPS module cannot receive a GPS signal. To aid in these scenarios, an update was made to the GTU7 module to support "fake" data returned similar to real data. This can be useful for testing purposes, or to gain familiarity with what to expect as a response.

If you want to generate fake data, use the following syntax for either GPGGA data or GPRMC data. Note the use of `fake=True` being passed in.

> :information_source: **TypeError: unexpected keyword argument 'fake'**  
	The fake data feature was added to the GTU7 module in an update. If you encounter the unexpected argument error, follow the steps earlier in the lesson on installing the GTU7 driver, ensuring you are using the latest copy of the driver located in this project.

```python
gpgga_data = gps_module.gpgga(fake=True)
gprmc_data = gps_module.gprmc(fake=True)
```

**Congratulations! You have successfully completed Lesson 4.**

<br><br>

## Want more?
If you have finished with the base lesson, check out the items below.
<br><br>

Update the code to do any/all of the following:
1. Reformat the printed output to a format of your liking
1. Reformat the printed output to be simply a list of the information
1. Print out another module data point (**Hint:** look at the driver...) 😁

Things to think about, validate, and/or try:
* What are the units/formats of the module output? 🤔
* How accurate is the readout of the module? 
    * Coordinates?
    * Date?
    * Time?
* What other readings are available from the module? (**Hint:** look at the driver...) 😏
* Understand more about [GPS data and NMEA sentence information](https://aprs.gids.nl/nmea/).
* What is UART and how are we using it? 😵
* Research [Google's Geocoding API and understand how we can use latitude and longitude to perform a reverse geocoding lookup](https://developers.google.com/maps/documentation/geocoding/requests-reverse-geocoding) to retrieve a human readable address for our location data

## Challenge 
Modify your code to handle exceptions.

This challenge will introduce you to using  [Python Try Except](https://www.w3schools.com/python/python_try_except.asp) code blocks for exception handling. The Try Except code block is very useful in handling errors and exceptions from functions or code attempts. In its basic implementation, this code block tries something, except if something unexpected happens (like an error), try something else. If all else fails, finally take one last action.

A successful implementation of this code will result in the following:
* A Try Except code block handling the following error: `IndexError: list index out of range`
  HINT: One method of recreating this error is by flipping the TX and RX wires.
* A response providing troubleshooting tips to the user for if this error is encountered.

As you think through this code, also consider how it might be applied to previous lessons. Similarly, keep this code in mind for future lessons. It is a useful approach for offering more informed responses to errors, or alternatively taking new actions if an error is encountered.

<details>
<summary>Expand to see an example using a Try Catch to handle an exception</summary>

```python
# Import all needed libraries
from machine import Pin, UART
import time
from drivers import gtu7

if __name__ == "__main__" :
    
    # Define our UART(Universal Asynchronous Receiver/Transmitter)
    uart = UART(1,
                baudrate=9600,
                timeout=3600,
                tx=Pin(4),
                rx=Pin(5))
    
    # Loop for GPS coordinates
    while True:
        gps_module = gtu7.GTU7(uart)

        gpgga_data = gps_module.gpgga()
        
        try: # Try printing the data.
            print("Latitude:\t{0}\nLongitude:\t{1}\nSatellites:\t{2}\nTime:\t\t{3}\n".
                  format(gpgga_data[1], gpgga_data[2], gpgga_data[3], gpgga_data[0]))
        except IndexError as e: # We are capturing the specific `IndexError` exception. However, you can capture other
                                # exceptions as well. View the Troubleshooting section for this lesson and think
                                # about how you might add more exception handling
            print("No data returned from GPS module. Ensure wiring is correct.")

        time.sleep(5)

```
</details>

## Troubleshooting

* `ERROR: No GPS data returned`

  If you are not receiving GPS data, the following may be the case:

  * You have the RX and TX connections reversed. Be sure the TX on the GT-U7 goes to the UART RX on the Pico, and the RX on the GT-U7 goes to the UART TX on the Pico.
  * Your GPS device has not yet established a connection with satellites. Be patient, this can sometimes take several minutes.
  * In some cases GPS data is returned, in other cases it is not. Expect to see some intervals fail while other succeed. Again, this is dependent on the GPS having a good connection with satellites.
  * If after several minutes you are still not receiving GPS data, ensure you are in a location where the GPS module can successfully connect. Move to a higher floor in your location, or near a window.

* `ERROR: No module named (drivers, bmp180, ...)`
    
    If you see this error it means Python is not able to locate a module to be imported. This can occur because the version of MicroPyhon you are using does not support the module you are trying to import. Specifically for this lesson it likely applies to the `drivers` step. Ensure the `drivers` folder and its contents, `gtu7.py` and `__init__.py`, are saved to the Raspberry Pi Pico device and _not_ your computer. 
    
    Also be aware the case-sensitivity of the `drivers` folder name (lower case) and how its referenced in your Python code. Be sure everything is in lower case.

    Example error message:
    ```sh
    Traceback (most recent call last):
      File "<stdin>", line 2, in <module>
    ImportError: no module named 'drivers'
    ```

* `ERROR: IndexError: list index out of range`
    
    Specific to the code in this lesson, this error occurs when we attempt to format the GPS data for printed output, but there is no data to format. In other words we are attempted to format an empty array. The cause for no data being returned could be related to:
    1. No GPS signal. See first troubleshooting error for more information to help with this.

    Example error message:
    ```sh
    Traceback (most recent call last):
      File "<stdin>", line 22, in <module>
    IndexError: list index out of range
    ```

* `ERROR: TypeError: unexpected keyword argument 'fake'`
    
    On occasion the drivers will be updated. The GTU7 driver received an update that allowed fake data to be created in the scenario where GPS signal cannot be acquired. If the user attempts to pass in `fake=True` and receives this error, the GTU7 driver is out of date. Follow the steps in the lesson above to install the GTU7 driver, overwriting the existing version on your Pi Pico.

    Example error message:
    ```sh
    Traceback (most recent call last):
      File "<stdin>", line 19, in <module>
    TypeError: unexpected keyword argument 'fake'
    ```

## Need help?
Watch the walk-through [video](./docs/videos/Lesson4.mp4?raw=true) for guidance!

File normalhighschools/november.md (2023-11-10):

# November Materials

## Goals

- Students will learn to think systematically to solve problems which is the core of learning how to program
- Use resources available to solve problems
- Work as a small group to spread the work
- Present the research in the December session
<br><br><br>
## Game Plan

Below are topics to be assigned to small groups in the classrooms. The small group will need to research details and evaluate where problems may arise and how to proactively solve them. Mentors can help facilitate if students get stuck! Each sub section is one per group to be assigned by the teacher / lead mentor.

-	There are 7 main topics and the largest class has 7 teams. This allows one major topic for every team
    -	If the class has less than 7 teams, choose from the topics and assign to teams
    -	The teacher and lead mentor can divide topics across the teams as they see fit
    -	If the lead mentor can report back which mentor has what topics that would be helpful
-	Teams are welcome to explore the topic beyond the thought starters I have listed
-	Research will be needed, use ALL resources available to research as a team (cell phones, laptops, etc. to search the internet). These topics should EASILY fill the class period with discussion
-	Each team is to present in December their findings / solutions to the issues they were assigned
    -	It is at the teacher’s discretion how they present to the class (open discussion, PowerPoints, etc.)
    -	The December session will be spend doing the share out taking the entire class time
        -	Teams will need to be prepared BEFORE the December session; no time will be provided in the December session for prep
<br><br><br>
### Temperature issues:
  - The balloon will travel from 110,000 feet. What temperatures will it encounter though the flight column
  - What temperature limitations would an Arduino UNO, Raspberry PICO, Rechargable battery, etc have?
  - Reverse, what would high temperature limitations be?
  - How can things be tested on the ground?
  - How to protect things thermally?
  - Will anythign used produce heat?

### Power / Battery issues:
  - Some assumptions / constraints:
    - Average flight time is 4 hours
    - Research average temperatures in the upper atmosphere
    - [An AA size dry cell has a capacity of about 2,000 to 3,000 milliampere hours](https://en.wikipedia.org/wiki/Ampere_hour)
    - We need to be around 4lbs total for our payload EVERYTHING included below the balloon (weight is a BIG concern)
  - What kinds of battereries can we use and the pro's and Con's of each (rechargable (different kinds), dry cell, battery size, weight 
  - How much capacity is needed for the flight running the following items:
    - 3 [Action Cameras](https://smile.amazon.com/AKASO-Control-Waterproof-Adjustable-Accessories/dp/B07J4TNYV8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)
      - 600 [MaH](https://en.wikipedia.org/wiki/Ampere_hour) per camera per hour of recording
    - One Arduino Uno 
      - The Arduino Uno board draws about 42 mA assuming no power draw from sensors or other components needed in your system. With a minimum supply voltage of 7 volts, the power consumption of the board is therefore 0.29 Watts
    - [Tracker](http://qrp-labs.com/lightaprsw2)
      - Assume same power as Arduino 
  - Any other items of note to share from your research or further questions?

### Tracking:
  - How can we track the balloon in flight?
    - Telemetry broadcasting of extra sensors is a plus, at a minimum we need latitude, longitude, and altitude near real time
    - Need for recovery of the payload
      - Video
      - Electronics
  - Pro's and con's of each solution researched?
    - Many items should be accounted for like is it legal, does it need to face a certain direction, does it need a clear line of site to the sky, power needs, weight, etc.
    - Is there a way to record the flight data for retrieval later for each option?
    - How would we mount it in the foam cooler (12"x12"x12")
    - Can there be backup tracking options?
  - Any other items of note to share from your research or further questions?

### Laws, regulations, and safety
  - What laws and regulations are we restricted to by the FAA?
    - Payload weight
    - Rigging cords
    - Notifications
  - Who would we notify of our flight? (NOTAMs (Notice to Airmen) via the FAA’s Federal NOTAM System)
  - What threats could influence the safety of a flight and how might the risk be elminated or mitigated? 
  - Any other items of note to share from your research or further questions?

### Cameras
  - What area should be recorded during the flight and why
  - What kind of camera should we use
    - Power usage, weight, orientation, weather resistant or easy way to make it weather proof, etc
    - What is the operating temperature range
    - Pro's and con's of each solution researched?
  - Will there be a problem with [RFI](https://en.wikipedia.org/wiki/Radio_frequency)? What measures can be taken to prevent issues with RFI?
  - How to mount them in the foam cooler (12"x12"x12")
  - Any other items of note to share from your research or further questions?

### Payload stabilization and rigging:
  - How to retrieve is caught in a tree, roof, other obstruction
  - How do we keep the ballooon from spinning too much?
  - Tangle hazards that would prevent the parachute from working
  - Proposed methods to attach the balloon to the payload?
    - Assumption is the payload is a foam cooler (12'x12'x12')
  - Any other items of note to share from your research or further questions?

### Landing prediction:
  - How can we plan for approximate landing location of the HAB
  - What factors impact or go into the prediction
  - When should the prediction be run
  - Any other items of note to share from your research or further questions?

### Lift gas:
  - Options for lift gas in our balloon
    - Safety concerns, availability, cost, where to buy, quality, regulations
    - Pros and cons
  - How much do we need for a [1600 gram balloon](https://www.kaymont.com/_files/ugd/a13aac_8b84755b308c473b8ac99f1dc39b80e1.pdf) carrying a 4lb payload
  - How do we know how much gas we dispnsed from the tank
  - Any other items of note to share from your research or further questions?

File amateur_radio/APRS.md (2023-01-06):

# Automatic Packet Reporting System (APRS)

## Introduction

APRS is an amateur radio-based system for real time digital communication of locale information of 'immediate value'.  APRS was designed to support rapid, reliable exchange of information for local, tactical real-time decisions, events, or communication nets.  The technology was developed in the late 1980s, and has been widely implemented in a variety of VHF/UHF amateur radios. 

It is designed to communicate all relevant information immediately to everyone (all stations and participants) to ensure the information shared is consistent.  Data can include Global Positioning System (GPS) coordinates, weather station data, text messages, announcements, queries, and other telemetry information that needs to be shared. The data sent over APRS is (often) displayed and viewed on a map, showing the position of stations, objects, tracks of moving objects, weather, and other information to assist search and rescue and direction finding.  

Due to its design, it makes it ideal for high-altitude balloon tracking as it provides a means to communicate all information necessary to identify the current location and altitude of the balloon.

## APRS Tracker

## APRS Messages

Information is maintained and refreshed at regular intervals. APRS uses a standard message types / formats to communicate POSITION, STATUS, MESSAGES and QUERIES, but also to accurately display map objects such as vehicles and stations.  Because it is a shared telecommunication medium (wireless RF network), guidelines on use, and how often stations should check in are defined.  For example, it is recommended stations limit how often they beacon to avoid creating unnecessary congestion for high or emergency priority messages.  Stations that need to regularly transmit position updates, it is generally recommended their beacon interval be no less than every 60 to 90 seconds.

Over the APRS network, all messages are delivered in real-time to all stations and recipients.  Messages are not stored and forwarded, but retried/relayed until time out is reached. The delivery of these messages is global, since APRS-IS distributes all packets over the internet to all other iGate repeaters in the world.  And messages will actually go back to wireless RF via any iGate that is near the intended recipent.

Below are a couple important message types:

### Telemetry Messages (Position/Object/Item)

APRS telemetry messages relay position, object, and item information containing latitude, longtitude, a symbol to be displayed on a map, and optional user fields.  These fields can include altitude, course, speed, radiated power, equipment voltage, antenna height, above average terrain, antenna gain, voice operating frequency, and more.  

For high-altitude balloon trackers, there is generally opportunity to include custom fields in telemetry messages to relay situation information about the payload and flight.  Temperature, pressure, battery voltage, and message count are common examples.  Some trackers support the ability to attach external sensors via I2C that can provide other information to relay.  The latitude and longitude coordinatres are automatically derive from GPS module included in the tracker.  

These fields along with message handling fields are encoded into a single string, which is transmitted at low power by the tracker.

**Example Telemetry Map**
(flight path image goes here)

**Example Raw Message** <br>
```BR4XZ-10>AP51DW,WIDE1-1,WIDE2-1,qAS,BR4XZ-11:!3415.83N/11716.40ErXuZhou APRS 144.640Mhz 45W 13.8V  20.8C```

**Example External Sensor** <br>
(bmp280 sensor image goes here)

**Example Raw Message** <br>
```KW9D-11>APLIGA,N9ULL*,WIDE2-1,qAR,N9NWI-1:/151926h4032.58N/08855.34WO321/021/A=002143 00168H 30.1C 941.hPa 16.1C 945.hPa 44.9%```

### Status Messages (Comments)

APRS status messages follow a free-form format that allows each station to annouce other information that should be relayed to participants.  This information could be current mission, application, contact information, or any other information or data of immediate value surrounding the activities occuring.  Status messages can also be used for point-to-point communication, sending a message directed to a specific recipient.  

Status messages can be used by high-altitude balloon trackers to relay the school name, class, and other info about the high-altitude balloon project.  Additionally, status messages can relay health information about the tracker and equipment included in the payload.

Other uses for status messages are bulletins and announcements.  Bulletins and Announcements are treated specially by APRS and are meant to be display on a single 'community Bulletin board'.  This bulletin board is fixed size with all bulletins posted to the community, sorted for display.  The intent again is to ensure all participants are seeing the same information at the same time. 

## APRS Technical Details

APRS in its most widely used form, uses data transport over the AX.25 protocol on the 2-meter (144 Mhz to 148 Mhz) Amateur Radio band, using 1,200-bits/second Bell 202 modems.  The modems, or terminal node controllers (TNCs), generate two audio tones performing Audio Frequency Shift Keying (AFSK) to encode data, sent and received by handheld, mobile and base station radios.  For High Altitude Balloon flights, a small lightweight tracker is utilized.

Each APRS packet transmitted by a station may be received and relayed by a local digital repeater, or "digipeater".  This is especially important for mobile stations, such as those in vehicles.  In the United States, there is an extensive "digipeater" network providing transport and relay of APRS packets to ensure information is re-transmitted and received by all area participants.  Many digipeaters have Internet Gateway (iGates) connecting the on-the-air APRS with the APRS Internet System (APRS-IS) network which provides a worldwide high-bandwidth backbone for data sharing.  This allows APRS data to be shared with APRS websites, such as [APRS.fi](https://www.apfs.fi/) and others, for web-based aggregation and mapping.

## APRS Mobile Stations
The two images below should give you an idea of the kinds of information available to the operator on a APRS radio. On the left is the Kenwood D710 radio showing the station list, and on the right is the attached GPS map display showing the location of other APRS stations.

| **Raw Messages** | **GPS Map** |
| :----------: | :-----: |
| <img src="http://www.aprs.org/D7xx/AB9FXd710list1.JPG" width="450" /> | <img src="http://www.aprs.org/avmap/AVMAPg5_new_iconXx.JPG" width="500" /> |

<br/>

<details>
<summary><b>More Information</b></summary>

### APRS Frequencies Globally
Different frequencies are allocated for APRS across the globe.  For pico-balloon flights that maybe traveling across international boundaries, APRS geofencing must be supported by the tracker to ensure messages continue to be received.

![Frequencies by geographic area](http://www.aprs.org/maps/APRSVHFworldmapXx.jpg)

### APRS Digipeater PATH Relay

PATH settings determine what kind and how many digipeaters will be used to relay packets to their destination.  For all High-Altitude Balloon (HAB) and Pico-Balloon flights, WIDE-1 path settings are the guideline since multiple digipeater stations on the ground may receive APRS data transmitted.

<img src="http://www.aprs.net.au/sites/default/files/Digi-Demo.gif" />

</details>

## References

[APRS Overview and more information](http://www.aprs.org/)
[What is AFSK](https://www.notblackmagic.com/bitsnpieces/afsk//#what-is-afsk)
[2-Meter Amateur Radio Band](https://en.wikipedia.org/wiki/2-meter_band)

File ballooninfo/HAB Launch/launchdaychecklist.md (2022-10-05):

# Launch Day Checklist

## Packing list:

### Launch site protection and tools 
- Tarp
- Stakes for the tarp
- Gloves for anyone touching the balloon
- Helium bottle (2)
- Helium regulator
- [Balloon filler](https://the-rocketman.com/weather-balloon-inflator-2/)
- [Lift scale](https://the-rocketman.com/weather-balloon-inflator-2/)
- Fish scale (backup)
- Tether - Tank to balloon
- Tether - tank to scale
- Tether - scale to filler neck
- [PVC coupler](https://www.menards.com/main/plumbing/pipe-fittings/pvc-pipe-fittings/nibco-reg-socket-pvc-coupling/f00020t/p-1444449169639-c-8571.htm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)
- Duct tape
- Packing tape
- Electircal tape
- Zip ties heavy
- zip ties light
- side cutters
- wrench for regulator

### Balloon and payload
- [Ballon (2)](https://www.kaymont.com/product-page/hab-1500)
- [Parachute](https://the-rocketman.com/recovery-html/)
- [Rigging line (3)](https://the-rocketman.com/recovery-shock-cord-habs/)
- [Payload harness (2)](https://the-rocketman.com/4-point-recovery-harness-for-habs/)
- Payload boxes

### Payload contents
- [Batteries](https://smile.amazon.com/Energizer-Lithium-Batteries-Ultimate-Battery/dp/B01C4PP8FK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)
- [Battery holders](https://smile.amazon.com/gp/product/B08B86WYL3/ref=ewc_pr_img_2?smid=AJJYA8M5YMCKV&psc=1)
- [Buc converter]()
- USB splitter cable (2)
- Cameras (3)
- Crash alarm

## Tasks

### Prepare the balloon
- Setup tarp and stake
- Attach regulator and filler to the helium tank
- Attach Tethers
- Insert PVC coupler in the ballon neck
  - Fasten with zip ties
    - Ensure payload attachment loops are attached in the zip ties
- Attach the balloon to the filler
  - Tape to the filler with electrical tape
    - Leave tag end to unwrap
- Attach scale to tethers and test

### Ready payload
- Ensure batteries are in holders and secured in payload
- Ensure cameras are operational and memory cards are wiped
- Attach batteries to cameras
- Test quick recording and play back
- Attach cameras to the cones and tape in place
- Power on trackers
  - Test tracker / verify communcation
  - Attach to the payload box
  - Power down
- Attach batteries to payload box
- doublecheck payload harness is secure
- Attach payload(s) to rigging line
- Attach rigging line to parachute
- Attache parachute to balloon
- Ensure the payload train is laid out down wind so the balloon picks it up as it rises aftr launch
- Make sure if found info is labeled on the outside and included inside (ziploc)

### Ready to launch
- Review who is doing what
  - Make sure everyone knows the process
  - Answer any and all questions NOW
- Fill balloon
  - Ensure the balloon is managed by people and or bed sheet / blanket over it
  - Anyone touching the balloon should be wearing nitril / vinyl gloves
  - validate lift per [calculator](http://tools.highaltitudescience.com/#)
- Ensure payload is powered on
  - Cameras
    - Recording (triple check)
  - Trackers
  - Alarm 
- Ensure payload is secured (packing tape)
- Doublecheck rigging lines are secure and tug tested
  - Payload harness to rigging
  - Rigging to parachute
  - Parachute to balloon neck
- Pickup all non essential gear and move out of the way
- Zip tie above filler neck (2x) and tape
- Detach tape sealing ballon to the filler
- Zip tie below filler neck (2x) and tape
- Detach tether for scales
  - Double check lift one last time first
- Move the baloon clear of anything
- Pictures
- Countdown
- Release

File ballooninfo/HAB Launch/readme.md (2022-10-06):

# Here are some details about the launch

## Things we need to plan for

- Location of the launch
  - Plan for a spot for each wind condition
  - Clear of obstructions for both a good launch and one that may not go as planned
  - School map [Google Map](https://www.google.com/maps/@40.3948635,-89.2446226,1043m/data=!3m1!1e3)
- Weather
  - Preferably <10mph winds
  - Medium or no cloud cover
  - No rain for launch and ideally landing
- Run predictions
  - Launch coordinates 40.3948635 -89.2446226
  - [Links to prediciton calculators](https://www.overlookhorizon.com/how-to-launch-weather-balloons/flight-predictions/)
    - Cambridge University Spaceflight (CUSF) Landing Predictor
    - University of Southampton ASTRA High Altitude Balloon Planner
    - University of Michigan Flight Prediction Tool
    - University of Wyoming Trajectory Forecaster
    - S3 Research Flight Predictor
- Watch some videos to prep / know what to expect for students, mentors, staff
  - [Top 5 questons](https://www.overlookhorizon.com/top-5-questions-for-a-weather-balloon-engineer/)
  - [lift calculation](https://youtu.be/NxwlNnfKMHs)
  - [preparing a ballon for launch](https://youtu.be/6_06Q_eWta8)
  - [How to fill a balloon](https://youtu.be/5Z23L4QIgtQ)
  - [How to launcha balloon](https://youtu.be/x5NyTzCcn9E)

## Proof of concept launch

- We launched on 3/28 aproximately 4pm at Tri-Valley High school
- [The Story of Bartholomew The Space Potato](https://www.youtube.com/watch?v=lgF7glYxPEk&t=47s)
- [Video of launch](https://vimeo.com/693551736)
- [Overview from Tri-Valley](https://www.youtube.com/watch?v=9-vcuOU2RxY)
- [Highlights of Tri-Valley - flight footage](https://www.youtube.com/watch?v=hXOj18e2MYQ&t=10s)
- [Raw footage - complete flight](https://youtu.be/MibnktoN1XE)

## Lessons Learned (first draft)

- We need to have a second tracker incase one fails
- The address and phone numbers if found should be written and taped over to protect from weather
- The address and phone numbers should be in the payload in a ziploc
- Testing should be done exactly as the tracker will fly
  - perhaps even from a smaller balloon or drone etc
- Fix the scale issue we saw. Perhaps double checking with a jug of water / sand to the specified lift
  - lift should be 1.5 times the full payload (everythign under the balloon). I included the   
- The payload train should be laid out so the balloon picks it up as it travels with the wind (the train should point the same direction as the wind)
- Review what each user will do at launch before hand ensuring questions are answered ahead of time
- Setup more cameras to catch more angles
  - Mix up some with time lapse
- Use rigging lines for the payloads
- Use premade lines for attaching to the fill tank and lines to the scale to calculate the lift
- Use PVC coupler for mounting point. Zip Tie int h neck before filling attaching rigging loops

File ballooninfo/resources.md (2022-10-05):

# List of things to checkout to learn more!

## ***Amateur Radio***
You maybe asking why is this here? Well, the primary tracking system on the balloon uses a form of radio called APRS, without it you would never be able to find your baloon. There is some really cool nerdy stuff that has many scholorship oppportunties within the radio world (hint hint hint)!
- [ARRL](https://www.arl.org/)
- [APRS](http://aprs.org/) which you need a amateur licensce to operate.
- [LightAPRS-W (+WSPR) Tracker](http://qrp-labs.com/lightaprs-w.html)
- [Technician study webinar](https://youtu.be/0wwnOPaF1qI)

## ***Arduino*** - if you want to learn more about the Arduino platform chek out this video.
- [Arduino basics with hands on labs](https://youtu.be/fJWR7dBuc18)

## ***High Altitude Balloons*** - if you are intrested in learning even more about HABs check out some of the links below.
- [Crazy long video showing everything this person does to launch and lots of tricks](https://youtu.be/a42fEO0dZ0M)
- [Overlook Horizon - HAB HowTo](https://www.overlookhorizon.com/how-to-launch-weather-balloons/)

## ***Python*** - is  a programing language that it widley used and very versitile.
- [Google Python Class](https://developers.google.com/edu/python)

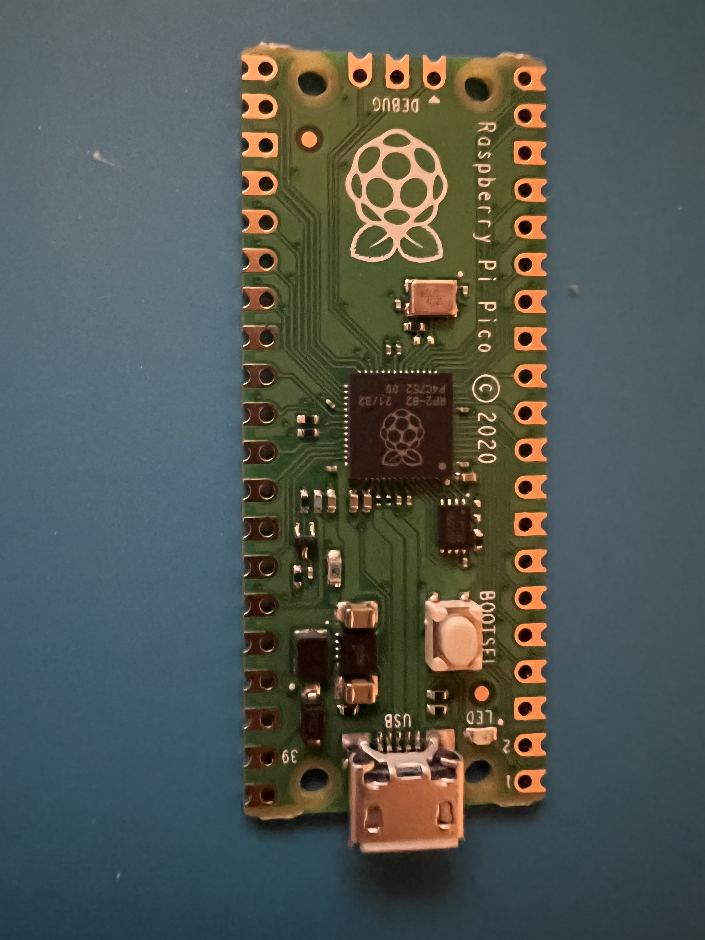
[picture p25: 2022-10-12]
python/raspberrypico/hardware/images/raspberrypico_front.jpg

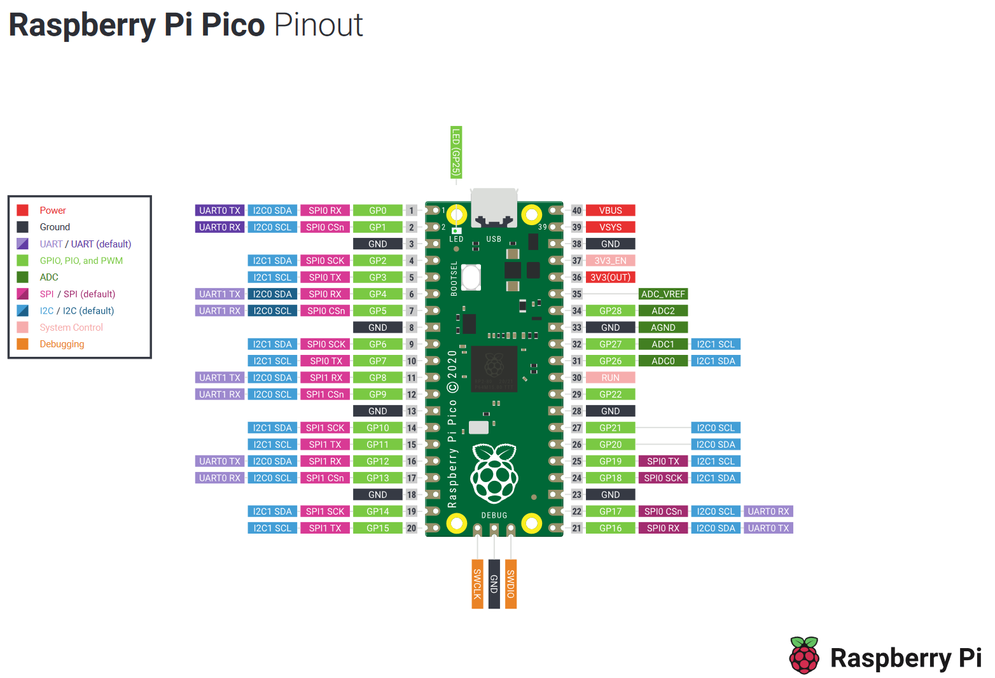
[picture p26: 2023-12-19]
python/raspberrypico/lesson-2/docs/images/raspberry-pi-pico-pinout.png

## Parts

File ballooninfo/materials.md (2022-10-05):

# Materials needed for this project will be broken down into catagories:

## Classroom Materials - Coding and Tracker project
- [UNO Project Super Starter Kit](https://smile.amazon.com/ELEGOO-Project-Tutorial-Controller-Projects/dp/B01D8KOZF4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)
- GPS module
- Weather sensor module
- Arduino SD card adapter
- Micro SD card

## High Altitude Balloon launch

### Equipment order:

| Action | Reuse?	| Notes |	Item	| Qty |  Unit Price | Total Price |
| - | - | - | - | - | - | - |
| Buy	| No	| We need 2 for the schools and 1 spare	| Balloon - HAB-1200	| 3	| 125	| 375| 
| Buy	| Yes	| These are pricey but they are high quality	| 5Ft. High Altitude Balloon Parachute	| 1	| 55.5	| 55.5| 
| Buy	| Yes	| We need 2 minimum but I said 3 incase we need to have multiple payload boxes	| Recovery Shock Cord - 15'	| 3	| 11	| 33| 
| Buy	| Yes	| We need 2 minimum but I said 3 incase we need to have multiple payload boxes	| 4 Point Recovery Harness	| 3	| 23.5 | 70.5| 
| Buy	| Yes	| This can be used to reduce the distance the balloon travels so its not recovered hours away	| Weather Balloon Chute Release	| 1	| 140	| 140| 
| I've purchased	| Yes	| This is needed to inflate the balloon from the tank. It reduces the pressure down	| Weather Balloon Inflator	| 1	| 75	| 75| 
| Buy| 	Yes	| This sounds an alarm when the payload doesn’t move for a period of time. This helps to locate it in the field	| Alarm	| 2	| 13	| 26| 
| Back ordered | Yes	| used to monitor the flight. It will report on two different bands one long range once close. We can use Tri-Valleys until one comes in stock	| APRS Tracker	| 1	| 115	| 115| 
| Buy	| Yes |	These are for recording from the cameras	| SD Cards - 128gb	| 5	| 27	| 135| 
| Buy	| Yes - Until we run out | Used to seal the balloon	| zip ties	| 1	| 15	| 15| 
| Buy	| Yes	| Generic GoPro's for recording side video and one up to catch the balloon burst	| Action cams	| 3	| 119	| 357| 
| Buy	| Yes	| Might be used to power cameras etc. | Battery pack	| 2	| 35	| 70| 
| Buy	| Yes	| This is used to find the payload once we arrive nearby	| SDR	| 2	| 42	| 84| 
| Buy	| Yes	| Powers the cams from the battery packs | USB cable for splitting power to cameras	| 2	| 7	| 14| 
| Buy	| Yes	| To protect the sharp ends of the zip ties from popping the balloon	| Wide electrical tape	| 1	| 9.5	| 9.5| 
| Buy	| Yes	| Two cameras for still pics from the payload	| Pi Camera	| 2	| 30	| 60| 
| I've got a guy in Downs to order from	| No	| Gas for the balloon	| Helium	| 2	| 300	| 600| 
| Buy	| Multiple use | Used to seal connections and cover some components	| Shrink Wrap	| 1	| 14	| 14| 
| Buy	| No	| Powers cameras and tracker. We need the premium Lithium cells to not stop working at -60c	| Batteries - Energizer lithium aa	| 4	| 33	| 132| 
| Buy	| Yes	| Holds batteries for camera and tracker	| 4 way battery holders | 4	| 6	| 8	| 48| 
| Buy	| Kind of	| Board to solder componentns so they don’t come loose when flying	| Arduino Project hats | 3	| 15	| 45| 
| | | | | | Total| 2473.5|

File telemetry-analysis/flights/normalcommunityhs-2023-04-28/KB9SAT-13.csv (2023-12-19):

Date | Time | TZ | Name | Path | GPS Time | Col 1 | Longitude | Col 2 | Latitude | Bearing | Speed | Altitude | HDOP | Temp | Pressue | Description | Total TxC | Telemetry TxC | Status TxC | Icon | Column13 | Column14 | Column15 | Column16 | Column17 | Column18 | Column19 | Column20 | Column21 | Column22 | Column23
4/28/2023 | 9:12:08 AM | CDT: | KB9SAT-13 | APLIGA,WA9RES*,WIDE2-1,qAR,KC8RFE-2 | 141201 | 4032.03 | 40.3203 | 8854.82 | -88.5482 | 41 | 6 | 2145 | 00169H | 43.5C | 1699hPa | Atlas-7 |  |  |  | 190
4/28/2023 | 9:13:08 AM | CDT: | KB9SAT-13 | APLIGA,WIDE2-1,qAR,KC8RFE-3 | 141302 | 4031.97 | 40.3197 | 8854.76 | -88.5476 | 197 | 11 | 3336 | 00111H | 43.7C | 1674hPa | Atlas-7 |  |  |  | 190
4/28/2023 | 9:14:09 AM | CDT: | KB9SAT-13 | APLIGA,WIDE2-1,qAR,KA3BQE | 141403 | 4031.83 | 40.3183 | 8854.83 | -88.5483 | 202 | 16 | 4423 | 00098H | 43.7C | 1648hPa | Atlas-7 |  |  |  | 190
4/28/2023 | 9:15:10 AM | CDT: | KB9SAT-13 | APLIGA,WIDE2-1,qAR,KA3BQE | 141504 | 4031.68 | 40.3168 | 8854.9 | -88.549 | 155 | 10 | 5533 | 00097H | 43.8C | 1623hPa | Atlas-7 |  |  |  | 190
4/28/2023 | 9:16:11 AM | CDT: | KB9SAT-13 | APLIGA,WIDE2-1,qAO,KS9A-10 | 141605 | 4031.5 | 40.315 | 8855.01 | -88.5501 | 182 | 15 | 6685 | 00093H | 43.7C | 1590hPa | Atlas-7 |  |  |  | 190
4/28/2023 | 9:17:12 AM | CDT: | KB9SAT-13 | APLIGA,WIDE2-1,qAO,KS9A-10 | 141706 | 4031.26 | 40.3126 | 8855.2 | -88.552 | 211 | 22 | 7787 | 00115H | 43.6C | 1557hPa | Atlas-7 |  |  |  | 190
4/28/2023 | 9:18:13 AM | CDT: | KB9SAT-13 | APLIGA,WIDE2-1,qAR,KC8RFE-3 | 141807 | 4031.05 | 40.3105 | 8855.35 | -88.5535 | 259 | 7 | 8888 | 00248H | 43.5C | 1526hPa | Atlas-7 |  |  |  | 190
4/28/2023 | 9:19:15 AM | CDT: | KB9SAT-13 | APLIGA,W9AZ-1,WIDE2*,qAR,K9MQ-1 | 141908 | 4030.82 | 40.3082 | 8855.51 | -88.5551 | 176 | 14 | 10032 | 00097H | 43.4C | 1496hPa | Atlas-7 |  |  |  | 190
4/28/2023 | 9:20:15 AM | CDT: | KB9SAT-13 | APLIGA,WIDE2-1,qAR,WB9EOC-10 | 142009 | 4030.59 | 40.3059 | 8855.67 | -88.5567 | 231 | 22 | 11251 | 00104H | 43.1C | 1461hPa | Atlas-7 |  |  |  | 190
4/28/2023 | 9:20:50 AM | CDT: | KB9SAT-13 | APLIGA,WIDE2-1,qAO,KS9A-10 |  |  |  |  |  |  |  |  | 6.01V | 07S | 00104H | 00000000F | 0148T | 0110T | 0038T | Atlas-7
4/28/2023 | 9:20:50 AM | CDT: | KB9SAT-13 | APLIGA,WIDE2-1,qAR,W9PFD |  |  |  |  |  |  |  |  | 6.01V | 07S | 00104H | 00000000F | 0148T | 0110T | 0038T | Atlas-7 |  |  |  |  |  |  |  | [Unsupported | packet | format]
4/28/2023 | 9:21:10 AM | CDT: | KB9SAT-13 | APLIGA,WIDE2-1,qAR,KC8RFE-3 |  |  |  |  |  |  |  |  | Community | High | School | IL | STEM
4/28/2023 | 9:21:10 AM | CDT: | KB9SAT-13 | APLIGA,WIDE2-1,qAR,W9PFD |  |  |  |  |  |  |  |  | Community | High | School | IL | STEM | [Unsupported | packet | format]
4/28/2023 | 9:21:29 AM | CDT: | KB9SAT-13 | APLIGA,WIDE2-1,qAR,KC8RFE-3 |  |  |  |  |  |  |  |  | Hour | - | Barry | the | Barometric | Balloon
4/28/2023 | 9:21:29 AM | CDT: | KB9SAT-13 | APLIGA,WIDE2-1,qAR,W9PFD |  |  |  |  |  |  |  |  | Hour | - | Barry | the | Barometric | Balloon | [Unsupported | packet | format]
4/28/2023 | 9:21:59 AM | CDT: | KB9SAT-13 | APLIGA,WIDE2-1,qAO,KS9A-10 | 142153 | 4030.16 | 40.3016 | 8856.02 | -88.5602 | 211 | 19 | 13188 | 00092H | 43.4C | 1438hPa | Atlas-7 |  |  |  | 190
4/28/2023 | 9:23:00 AM | CDT: | KB9SAT-13 | APLIGA,WIDE2-1,qAO,KS9A-10 | 142254 | 4030.01 | 40.3001 | 8855.92 | -88.5592 | 115 | 6 | 14275 | 00170H | 42.9C | 1390hPa | Atlas-7 |  |  |  | 190
4/28/2023 | 9:24:01 AM | CDT: | KB9SAT-13 | APLIGA,WIDE2-1,qAR,KC8RFE-2 | 142355 | 4029.86 | 40.2986 | 8855.9 | -88.559 | 138 | 14 | 15436 | 00093H | 42.4C | 1347hPa | Atlas-7 |  |  |  | 190
4/28/2023 | 9:26:03 AM | CDT: | KB9SAT-13 | APLIGA,WIDE2-1,qAO,KS9A-10 | 142557 | 4029.65 | 40.2965 | 8855.66 | -88.5566 | 193 | 10 | 17579 | 00127H | 41.5C | 1265hPa | Atlas-7 |  |  |  | 190
4/28/2023 | 9:27:04 AM | CDT: | KB9SAT-13 | APLIGA,WIDE2-1,qAO,KS9A-10 | 142658 | 4029.55 | 40.2955 | 8855.44 | -88.5544 | 138 | 17 | 18777 | 00099H | 41.1C | 1226hPa | Atlas-7 |  |  |  | 190
4/28/2023 | 9:28:05 AM | CDT: | KB9SAT-13 | APLIGA,WIDE2-1,qAO,KS9A-10 | 142759 | 4029.49 | 40.2949 | 8855.18 | -88.5518 | 290 | 5 | 20003 | 00116H | 40.6C | 1184hPa | Atlas-7 |  |  |  | 190
4/28/2023 | 9:29:06 AM | CDT: | KB9SAT-13 | APLIGA,WIDE2-1,qAO,KS9A-10 | 142900 | 4029.45 | 40.2945 | 8855.03 | -88.5503 | 73 | 19 | 21189 | 00101H | 40.1C | 1144hPa | Atlas-7 |  |  |  | 190
4/28/2023 | 9:30:07 AM | CDT: | KB9SAT-13 | APLIGA,WIDE2-1,qAO,KS9A-10 | 143001 | 4029.47 | 40.2947 | 8854.91 | -88.5491 | 73 | 4 | 22398 | 00151H | 39.6C | 1103hPa | Atlas-7 |  |  |  | 190
4/28/2023 | 9:30:42 AM | CDT: | KB9SAT-13 | APLIGA,WIDE2-1,qAR,KC8RFE-3 |  |  |  |  |  |  |  |  | 6.02V | 06S | 00151H | 00000000F | 0160T | 0119T | 0041T | Atlas-7
4/28/2023 | 9:30:42 AM | CDT: | KB9SAT-13 | APLIGA,WIDE2-1,qAR,W9PFD |  |  |  |  |  |  |  |  | 6.02V | 06S | 00151H | 00000000F | 0160T | 0119T | 0041T | Atlas-7 |  |  |  |  |  |  |  | [Unsupported | packet | format]
4/28/2023 | 9:31:02 AM | CDT: | KB9SAT-13 | APLIGA,WIDE2-1,qAR,KC8RFE-3 |  |  |  |  |  |  |  |  | Community | High | School | IL | STEM
4/28/2023 | 9:31:02 AM | CDT: | KB9SAT-13 | APLIGA,WIDE2-1,qAR,W9PFD |  |  |  |  |  |  |  |  | Community | High | School | IL | STEM | [Unsupported | packet | format]
4/28/2023 | 9:31:21 AM | CDT: | KB9SAT-13 | APLIGA,WIDE2-1,qAO,KS9A-10 |  |  |  |  |  |  |  |  | Hour | - | Barry | the | Barometric | Balloon
4/28/2023 | 9:31:21 AM | CDT: | KB9SAT-13 | APLIGA,WIDE2-1,qAR,W9PFD |  |  |  |  |  |  |  |  | Hour | - | Barry | the | Barometric | Balloon | [Unsupported | packet | format]
4/28/2023 | 9:31:51 AM | CDT: | KB9SAT-13 | APLIGA,WIDE2-1,qAO,KS9A-10 | 143145 | 4029.58 | 40.2958 | 8854.74 | -88.5474 | 62 | 6 | 24353 | 00097H | 39.7C | 1086hPa | Atlas-7 |  |  |  | 190
4/28/2023 | 9:32:52 AM | CDT: | KB9SAT-13 | APLIGA,WIDE2-1,qAO,KS9A-10 | 143246 | 4029.65 | 40.2965 | 8854.38 | -88.5438 | 70 | 25 | 25593 | 00179H | 38.9C | 1031hPa | Atlas-7 |  |  |  | 190
4/28/2023 | 9:33:53 AM | CDT: | KB9SAT-13 | APLIGA,WIDE2-1,qAO,KS9A-10 | 143347 | 4029.74 | 40.2974 | 8854.01 | -88.5401 | 53 | 18 | 26694 | 00133H | 38.1C | 980.hPa | Atlas-7 |  |  |  | 190
4/28/2023 | 9:34:54 AM | CDT: | KB9SAT-13 | APLIGA,WIDE2-1,qAR,KC8RFE-2 | 143448 | 4029.78 | 40.2978 | 8853.5 | -88.535 | 62 | 31 | 27918 | 00141H | 37.4C | 931.hPa | Atlas-7 |  |  |  | 190
4/28/2023 | 9:35:55 AM | CDT: | KB9SAT-13 | APLIGA,WIDE2-1,qAO,KS9A-10 | 143549 | 4029.92 | 40.2992 | 8853.03 | -88.5303 | 70 | 25 | 29250 | 00114H | 36.5C | 876.hPa | Atlas-7 |  |  |  | 190
4/28/2023 | 9:36:56 AM | CDT: | KB9SAT-13 | APLIGA,WIDE2-1,qAR,W9RCA-10 | 143650 | 4030.09 | 40.3009 | 8852.55 | -88.5255 | 43 | 23 | 30487 | 00092H | 35.7C | 826.hPa | Atlas-7 |  |  |  | 190
4/28/2023 | 9:37:57 AM | CDT: | KB9SAT-13 | APLIGA,WIDE2-1,qAO,KS9A-10 | 143751 | 4030.26 | 40.3026 | 8852.07 | -88.5207 | 92 | 25 | 31676 | 00125H | 35.0C | 782.hPa | Atlas-7 |  |  |  | 190
4/28/2023 | 9:38:58 AM | CDT: | KB9SAT-13 | APLIGA,WIDE2-1,qAR,KC8RFE-3 | 143852 | 4030.45 | 40.3045 | 8851.69 | -88.5169 | 33 | 18 | 32799 | 00108H | 34.3C | 736.hPa | Atlas-7 |  |  |  | 190
4/28/2023 | 9:39:59 AM | CDT: | KB9SAT-13 | APLIGA,WIDE2-1,qAO,KS9A-10 | 143953 | 4030.67 | 40.3067 | 8851.3 | -88.513 | 80 | 31 | 34112 | 00180H | 33.4C | 687.hPa | Atlas-7 |  |  |  | 190
4/28/2023 | 9:41:00 AM | CDT: | KB9SAT-13 | APLIGA,WIDE2-1,qAR,KX9A-1 | 144054 | 4030.87 | 40.3087 | 8850.67 | -88.5067 | 62 | 33 | 35338 | 00223H | 32.6C | 641.hPa | Atlas-7 |  |  |  | 190
4/28/2023 | 9:41:35 AM | CDT: | KB9SAT-13 | APLIGA,WIDE2-1,qAO,KS9A-10 |  |  |  |  |  |  |  |  | 6.02V | 06S | 00223H | 00000000F | 0173T | 0129T | 0044T | Atlas-7
4/28/2023 | 9:41:35 AM | CDT: | KB9SAT-13 | APLIGA,WIDE2-1,qAR,W9PFD |  |  |  |  |  |  |  |  | 6.02V | 06S | 00223H | 00000000F | 0173T | 0129T | 0044T | Atlas-7 |  |  |  |  |  |  |  | [Unsupported | packet | format]
4/28/2023 | 9:41:54 AM | CDT: | KB9SAT-13 | APLIGA,WIDE2-1,qAO,KS9A-10 |  |  |  |  |  |  |  |  | Community | High | School | IL | STEM
4/28/2023 | 9:41:54 AM | CDT: | KB9SAT-13 | APLIGA,WIDE2-1,qAR,W9PFD |  |  |  |  |  |  |  |  | Community | High | School | IL | STEM | [Unsupported | packet | format]
4/28/2023 | 9:42:14 AM | CDT: | KB9SAT-13 | APLIGA,WIDE2-1,qAR,KC8RFE-3 |  |  |  |  |  |  |  |  | Hour | - | Barry | the | Barometric | Balloon
4/28/2023 | 9:42:14 AM | CDT: | KB9SAT-13 | APLIGA,WIDE2-1,qAR,W9PFD |  |  |  |  |  |  |  |  | Hour | - | Barry | the | Barometric | Balloon | [Unsupported | packet | format]
4/28/2023 | 9:42:44 AM | CDT: | KB9SAT-13 | APLIGA,WIDE2-1,qAR,KA3BQE | 144238 | 4031.37 | 40.3137 | 8849.55 | -88.4955 | 80 | 44 | 37617 | 00132H | 31.8C | 596.hPa | Atlas-7 |  |  |  | 190
4/28/2023 | 9:43:45 AM | CDT: | KB9SAT-13 | APLIGA,WIDE2-1,qAR,KC8RFE-3 | 144339 | 4031.52 | 40.3152 | 8848.72 | -88.4872 | 61 | 24 | 38890 | 00106H | 30.7C | 539.hPa | Atlas-7 |  |  |  | 190
4/28/2023 | 9:45:47 AM | CDT: | KB9SAT-13 | APLIGA,WIDE2-1,qAO,AB9JJ-10 | 144541 | 4031.88 | 40.3188 | 8847.44 | -88.4744 | 65 | 25 | 41617 | 00172H | 28.8C | 439.hPa | Atlas-7 |  |  |  | 190
4/28/2023 | 9:46:48 AM | CDT: | KB9SAT-13 | APLIGA,WIDE2-1,qAR,W9DUA-1 | 144642 | 4032.1 | 40.321 | 8846.78 | -88.4678 | 77 | 17 | 42735 | 00163H | 28.1C | 402.hPa | Atlas-7 |  |  |  | 190
4/28/2023 | 9:47:49 AM | CDT: | KB9SAT-13 | APLIGA,WIDE2-1,qAR,KC8RFE-3 | 144743 | 4032.2 | 40.322 | 8846.18 | -88.4618 | 85 | 26 | 43947 | 00112H | 27.3C | 363.hPa | Atlas-7 |  |  |  | 190
4/28/2023 | 9:48:51 AM | CDT: | KB9SAT-13 | APLIGA,N8IYX-4,WIDE2*,qAR,AGUSTA | 144844 | 4032.37 | 40.3237 | 8845.53 | -88.4553 | 88 | 20 | 45052 | 00112H | 26.6C | 332.hPa | Atlas-7 |  |  |  | 190
4/28/2023 | 9:49:50 AM | CDT: | KB9SAT-13 | APLIGA,WIDE2-1,qAO,KS9A-10 | 144944 | 4032.44 | 40.3244 | 8844.88 | -88.4488 | 92 | 27 | 46142 | 00167H | 25.9C | 302.hPa | Atlas-7 |  |  |  | 190
4/28/2023 | 9:50:50 AM | CDT: | KB9SAT-13 | APLIGA,WIDE2-1,qAO,KS9A-10 | 145044 | 4032.46 | 40.3246 | 8844.26 | -88.4426 | 64 | 24 | 47105 | 00210H | 25.3C | 271.hPa | Atlas-7 |  |  |  | 190
4/28/2023 | 9:51:25 AM | CDT: | KB9SAT-13 | APLIGA,WIDE2-1,qAR,KX9A-1 |  |  |  |  |  |  |  |  | 6.01V | 05S | 00210H | 00000000F | 0185T | 0138T | 0047T | Atlas-7
4/28/2023 | 9:51:25 AM | CDT: | KB9SAT-13 | APLIGA,WIDE2-1,qAR,NB9M-1 |  |  |  |  |  |  |  |  | 6.01V | 05S | 00210H | 00000000F | 0185T | 0138T | 0047T | Atlas-7 |  |  |  |  |  |  |  | [Unsupported | packet | format]
4/28/2023 | 9:51:44 AM | CDT: | KB9SAT-13 | APLIGA,WIDE2-1,qAR,KC8RFE-3 |  |  |  |  |  |  |  |  | Community | High | School | IL | STEM
4/28/2023 | 9:52:04 AM | CDT: | KB9SAT-13 | APLIGA,WIDE2-1,qAO,KS9A-10 |  |  |  |  |  |  |  |  | Hour | - | Barry | the | Barometric | Balloon
4/28/2023 | 9:52:04 AM | CDT: | KB9SAT-13 | APLIGA,WIDE2-1,qAR,NB9M-1 |  |  |  |  |  |  |  |  | Hour | - | Barry | the | Barometric | Balloon | [Unsupported | packet | format]
4/28/2023 | 9:52:33 AM | CDT: | KB9SAT-13 | APLIGA,WIDE2-1,qAO,KS9A-10 | 145227 | 4032.72 | 40.3272 | 8843.41 | -88.4341 | 47 | 27 | 49083 | 00172H | 24.9C | 261.hPa | Atlas-7 |  |  |  | 190
4/28/2023 | 9:53:33 AM | CDT: | KB9SAT-13 | APLIGA,WIDE2-1,qAO,KS9A-10 | 145327 | 4032.94 | 40.3294 | 8842.87 | -88.4287 | 71 | 27 | 50160 | 00180H | 24.4C | 235.hPa | Atlas-7 |  |  |  | 190
4/28/2023 | 9:54:33 AM | CDT: | KB9SAT-13 | APLIGA,WIDE2-1,qAR,KC8RFE-3 | 145427 | 4033.19 | 40.3319 | 8842.21 | -88.4221 | 61 | 39 | 51229 | 00377H | 23.9C | 213.hPa | Atlas-7 |  |  |  | 190
4/28/2023 | 9:55:33 AM | CDT: | KB9SAT-13 | APLIGA,WIDE2-1,qAR,KC8RFE-3 | 145527 | 4033.31 | 40.3331 | 8841.66 | -88.4166 | 88 | 25 | 52231 | 00247H | 23.4C | 186.hPa | Atlas-7 |  |  |  | 190
4/28/2023 | 9:56:33 AM | CDT: | KB9SAT-13 | APLIGA,WIDE2-1,qAO,KS9A-10 | 145627 | 4033.47 | 40.3347 | 8841.04 | -88.4104 | 57 | 36 | 53386 | 00161H | 22.9C | 160.hPa | Atlas-7 |  |  |  | 190
4/28/2023 | 9:57:33 AM | CDT: | KB9SAT-13 | APLIGA,WIDE2-1,qAO,KS9A-10 | 145727 | 4033.65 | 40.3365 | 8840.24 | -88.4024 | 89 | 36 | 54436 | 00161H | 22.3C | 136.hPa | Atlas-7 |  |  |  | 190
4/28/2023 | 9:58:33 AM | CDT: | KB9SAT-13 | APLIGA,WIDE2-1,qAO,KS9A-10 | 145827 | 4033.72 | 40.3372 | 8839.44 | -88.3944 | 72 | 37 | 55477 | 00167H | 21.9C | 117.hPa | Atlas-7 |  |  |  | 190
4/28/2023 | 9:59:33 AM | CDT: | KB9SAT-13 | APLIGA,WIDE2-1,qAO,KS9A-10 | 145927 | 4033.75 | 40.3375 | 8838.82 | -88.3882 | 102 | 16 | 56618 | 00159H | 21.5C | 99.8hPa | Atlas-7 |  |  |  | 190
4/28/2023 | 10:00:33 AM | CDT: | KB9SAT-13 | APLIGA,WIDE2-1,qAO,KS9A-10 | 150027 | 4033.82 | 40.3382 | 8838.3 | -88.383 | 82 | 35 | 57695 | 00158H | 21.5C | 102.hPa | Atlas-7 |  |  |  | 190
4/28/2023 | 10:01:08 AM | CDT: | KB9SAT-13 | APLIGA,WIDE2-1,qAO,KS9A-10 |  |  |  |  |  |  |  |  | 5.97V | 07S | 00158H | 00000000F | 0197T | 0147T | 0050T | Atlas-7
4/28/2023 | 10:01:08 AM | CDT: | KB9SAT-13 | APLIGA,WIDE2-1,qAR,NB9M-1 |  |  |  |  |  |  |  |  | 5.97V | 07S | 00158H | 00000000F | 0197T | 0147T | 0050T | Atlas-7 |  |  |  |  |  |  |  | [Unsupported | packet | format]
4/28/2023 | 10:01:27 AM | CDT: | KB9SAT-13 | APLIGA,WIDE2-1,qAR,KC8RFE-3 |  |  |  |  |  |  |  |  | Community | High | School | IL | STEM
4/28/2023 | 10:01:27 AM | CDT: | KB9SAT-13 | APLIGA,WIDE2-1,qAR,W9PFD |  |  |  |  |  |  |  |  | Community | High | School | IL | STEM | [Unsupported | packet | format]
4/28/2023 | 10:01:47 AM | CDT: | KB9SAT-13 | APLIGA,WIDE2-1,qAO,KS9A-10 |  |  |  |  |  |  |  |  | Hour | - | Barry | the | Barometric | Balloon
4/28/2023 | 10:01:47 AM | CDT: | KB9SAT-13 | APLIGA,WIDE2-1,qAR,NB9M-1 |  |  |  |  |  |  |  |  | Hour | - | Barry | the | Barometric | Balloon | [Unsupported | packet | format]
4/28/2023 | 10:02:16 AM | CDT: | KB9SAT-13 | APLIGA,WIDE2-1,qAR,KA3BQE | 150210 | 4034.02 | 40.3402 | 8837.33 | -88.3733 | 72 | 29 | 59610 | 00164H | 21.6C | 110.hPa | Atlas-7 |  |  |  | 190
4/28/2023 | 10:03:16 AM | CDT: | KB9SAT-13 | APLIGA,WIDE2-1,qAO,KS9A-10 | 150310 | 4034.06 | 40.3406 | 8836.9 | -88.369 | 74 | 12 | 60723 | 00261H | 21.1C | 87.0hPa | Atlas-7 |  |  |  | 190
4/28/2023 | 10:04:16 AM | CDT: | KB9SAT-13 | APLIGA,WIDE2-1,qAO,KS9A-10 | 150410 | 4034.09 | 40.3409 | 8836.43 | -88.3643 | 85 | 29 | 61851 | 00220H | 21.1C | 86.9hPa | Atlas-7 |  |  |  | 190
4/28/2023 | 10:05:16 AM | CDT: | KB9SAT-13 | APLIGA,WIDE2-1,qAR,KX9A-1 | 150510 | 4034.16 | 40.3416 | 8836.04 | -88.3604 | 75 | 19 | 62915 | 00218H | 21.0C | 84.8hPa | Atlas-7 |  |  |  | 190
4/28/2023 | 10:06:16 AM | CDT: | KB9SAT-13 | APLIGA,WIDE2-1,qAO,KS9A-10 | 150610 | 4034.25 | 40.3425 | 8835.69 | -88.3569 | 61 | 30 | 64238 | 00215H | 20.8C | 75.5hPa | Atlas-7 |  |  |  | 190
4/28/2023 | 10:07:16 AM | CDT: | KB9SAT-13 | APLIGA,WIDE2-1,qAO,KS9A-10 | 150710 | 4034.25 | 40.3425 | 8835.35 | -88.3535 | 61 | 3 | 65390 | 00213H | 20.5C | 61.9hPa | Atlas-7 |  |  |  | 190
4/28/2023 | 10:08:16 AM | CDT: | KB9SAT-13 | APLIGA,WIDE2-1,qAO,KS9A-10 | 150810 | 4034.39 | 40.3439 | 8835.1 | -88.351 | 33 | 25 | 66509 | 00348H | 20.5C | 64.6hPa | Atlas-7 |  |  |  | 190
4/28/2023 | 10:09:16 AM | CDT: | KB9SAT-13 | APLIGA,WIDE2-1,qAO,KS9A-10 | 150910 | 4034.43 | 40.3443 | 8834.72 | -88.3472 | 122 | 26 | 67702 | 00208H | 20.4C | 59.2hPa | Atlas-7 |  |  |  | 190
4/28/2023 | 10:10:16 AM | CDT: | KB9SAT-13 | APLIGA,WIDE2-1,qAO,KS9A-10 | 151010 | 4034.33 | 40.3433 | 8834.43 | -88.3443 | 138 | 5 | 68922 | 00206H | 20.2C | 48.7hPa | Atlas-7 |  |  |  | 190
4/28/2023 | 10:10:51 AM | CDT: | KB9SAT-13 | APLIGA,WIDE2-1,qAO,KS9A-10 |  |  |  |  |  |  |  |  | 5.96V | 05S | 00206H | 00000000F | 0209T | 0156T | 0053T | Atlas-7
4/28/2023 | 10:10:51 AM | CDT: | KB9SAT-13 | APLIGA,WIDE2-1,qAR,NB9M-1 |  |  |  |  |  |  |  |  | 5.96V | 05S | 00206H | 00000000F | 0209T | 0156T | 0053T | Atlas-7 |  |  |  |  |  |  |  | [Unsupported | packet | format]
4/28/2023 | 10:11:10 AM | CDT: | KB9SAT-13 | APLIGA,WIDE2-1,qAR,K8EMA-4 |  |  |  |  |  |  |  |  | Community | High | School | IL | STEM
4/28/2023 | 10:11:10 AM | CDT: | KB9SAT-13 | APLIGA,WIDE2-1,qAR,W9PFD |  |  |  |  |  |  |  |  | Community | High | School | IL | STEM | [Unsupported | packet | format]
4/28/2023 | 10:11:30 AM | CDT: | KB9SAT-13 | APLIGA,WIDE2-1,qAO,KS9A-10 |  |  |  |  |  |  |  |  | Hour | - | Barry | the | Barometric | Balloon
4/28/2023 | 10:11:31 AM | CDT: | KB9SAT-13 | APLIGA,KS9A-10*,qAR,W9PFD |  |  |  |  |  |  |  |  | Hour | - | Barry | the | Barometric | Balloon | [Unsupported | packet | format]
4/28/2023 | 10:11:42 AM | CDT: | KB9SAT-13 | APLIGA,JAMTWP,WIDE2*,qAR,HOLLY |  |  |  |  |  |  |  |  | Community | High | School | IL | STEM
4/28/2023 | 10:11:59 AM | CDT: | KB9SAT-13 | APLIGA,WIDE2-1,qAO,KS9A-10 | 151153 | 4034.38 | 40.3438 | 8834.07 | -88.3407 | 130 | 8 | 70852 | 00201H | 20.5C | 67.9hPa | Atlas-7 |  |  |  | 190
4/28/2023 | 10:12:59 AM | CDT: | KB9SAT-13 | APLIGA,WIDE2-1,qAO,KS9A-10 | 151253 | 4034.33 | 40.3433 | 8833.87 | -88.3387 | 53 | 18 | 71999 | 00199H | 20.4C | 66.0hPa | Atlas-7 |  |  |  | 190
4/28/2023 | 10:13:59 AM | CDT: | KB9SAT-13 | APLIGA,WIDE2-1,qAR,N9VHT-3 | 151353 | 4034.34 | 40.3434 | 8833.77 | -88.3377 | 156 | 7 | 73237 | 00196H | 20.3C | 57.5hPa | Atlas-7 |  |  |  | 190
4/28/2023 | 10:14:59 AM | CDT: | KB9SAT-13 | APLIGA,WIDE2-1,qAO,KS9A-10 | 151453 | 4034.43 | 40.3443 | 8833.53 | -88.3353 | 319 | 9 | 74494 | 00193H | 20.2C | 53.7hPa | Atlas-7 |  |  |  | 190
4/28/2023 | 10:15:59 AM | CDT: | KB9SAT-13 | APLIGA,WIDE2-1,qAR,KC8RFE-3 | 151553 | 4034.35 | 40.3435 | 8833.47 | -88.3347 | 185 | 13 | 75844 | 00191H | 20.0C | 48.1hPa | Atlas-7 |  |  |  | 190
4/28/2023 | 10:16:41 AM | CDT: | KB9SAT-13 | APLIGA,JAMTWP,WIDE2*,qAR,HOLLY | 151553 | 4034.35 | 40.3435 | 8833.47 | -88.3347 | 185 | 13 | 75844 | 00191H | 20.0C | 48.1hPa | Atlas-7 |  |  |  | 190
4/28/2023 | 10:16:59 AM | CDT: | KB9SAT-13 | APLIGA,WIDE2-1,qAO,KS9A-10 | 151653 | 4034.31 | 40.3431 | 8833.42 | -88.3342 | 185 | 7 | 77129 | 00203H | 19.9C | 42.9hPa | Atlas-7 |  |  |  | 190
4/28/2023 | 10:17:59 AM | CDT: | KB9SAT-13 | APLIGA,WIDE2-1,qAO,KS9A-10 | 151753 | 4034.3 | 40.343 | 8833.27 | -88.3327 | 23 | 12 | 78428 | 00186H | 19.7C | 32.5hPa | Atlas-7 |  |  |  | 190
4/28/2023 | 10:18:59 AM | CDT: | KB9SAT-13 | APLIGA,WIDE2-1,qAR,KC8RFE-3 | 151853 | 4034.37 | 40.3437 | 8833.07 | -88.3307 | 79 | 20 | 79565 | 00184H | 19.8C | 35.7hPa | Atlas-7 |  |  |  | 190
4/28/2023 | 10:19:59 AM | CDT: | KB9SAT-13 | APLIGA,WIDE2-1,qAR,KD9EJE-1 | 151953 | 4034.45 | 40.3445 | 8832.79 | -88.3279 | 34 | 26 | 80792 | 00320H | 19.8C | 37.2hPa | Atlas-7 |  |  |  | 190
4/28/2023 | 10:20:59 AM | CDT: | KB9SAT-13 | APLIGA,WIDE2-1,qAO,KS9A-10 | 152053 | 4034.55 | 40.3455 | 8832.4 | -88.324 | 87 | 14 | 82057 | 00179H | 20.0C | 50.3hPa | Atlas-7 |  |  |  | 190
4/28/2023 | 10:21:34 AM | CDT: | KB9SAT-13 | APLIGA,WIDE2-1,qAR,KX9A-1 |  |  |  |  |  |  |  |  | 5.91V | 05S | 00179H | 00000000F | 0222T | 0166T | 0056T | Atlas-7
4/28/2023 | 10:21:53 AM | CDT: | KB9SAT-13 | APLIGA,WIDE2-1,qAR,WB9TLH-12 |  |  |  |  |  |  |  |  | Community | High | School | IL | STEM
4/28/2023 | 10:21:53 AM | CDT: | KB9SAT-13 | APLIGA,WIDE2-1,qAR,NB9M-1 |  |  |  |  |  |  |  |  | Community | High | School | IL | STEM | [Unsupported | packet | format]
4/28/2023 | 10:22:12 AM | CDT: | KB9SAT-13 | APLIGA,WIDE2-1,qAO,KS9A-10 |  |  |  |  |  |  |  |  | Hour | - | Barry | the | Barometric | Balloon
4/28/2023 | 10:22:13 AM | CDT: | KB9SAT-13 | APLIGA,WIDE2-1,qAR,W9PFD |  |  |  |  |  |  |  |  | Hour | - | Barry | the | Barometric | Balloon | [Unsupported | packet | format]
4/28/2023 | 10:22:42 AM | CDT: | KB9SAT-13 | APLIGA,WIDE2-1,qAR,KX9A-1 | 152236 | 4034.61 | 40.3461 | 8831.83 | -88.3183 | 78 | 30 | 84320 | 00271H | 20.8C | 96.7hPa | Atlas-7 |  |  |  | 190
4/28/2023 | 10:23:42 AM | CDT: | KB9SAT-13 | APLIGA,WIDE2-1,qAR,KC8RFE-3 | 152336 | 4034.71 | 40.3471 | 8831.41 | -88.3141 | 70 | 29 | 85487 | 00123H | 20.4C | 70.9hPa | Atlas-7 |  |  |  | 190
4/28/2023 | 10:24:42 AM | CDT: | KB9SAT-13 | APLIGA,WIDE2-1,qAR,W9YB-1 | 152436 | 4034.82 | 40.3482 | 8830.98 | -88.3098 | 31 | 27 | 86584 | 00124H | 20.1C | 58.2hPa | Atlas-7 |  |  |  | 190
4/28/2023 | 10:25:42 AM | CDT: | KB9SAT-13 | APLIGA,WIDE2-1,qAO,KS9A-10 | 152536 | 4034.9 | 40.349 | 8830.43 | -88.3043 | 86 | 30 | 87730 | 00139H | 20.1C | 56.6hPa | Atlas-7 |  |  |  | 190
4/28/2023 | 10:26:42 AM | CDT: | KB9SAT-13 | APLIGA,WIDE2-1,qAO,KS9A-10 | 152636 | 4034.86 | 40.3486 | 8829.76 | -88.2976 | 106 | 23 | 89026 | 00141H | 20.0C | 51.7hPa | Atlas-7 |  |  |  | 190
4/28/2023 | 10:27:42 AM | CDT: | KB9SAT-13 | APLIGA,WIDE2-1,qAR,KC8RFE-3 | 152736 | 4034.81 | 40.3481 | 8829.23 | -88.2923 | 65 | 26 | 90273 | 00127H | 20.1C | 57.0hPa | Atlas-7 |  |  |  | 190
4/28/2023 | 10:28:42 AM | CDT: | KB9SAT-13 | APLIGA,WIDE2-1,qAR,KO4FYC-1 | 152836 | 4034.88 | 40.3488 | 8828.6 | -88.286 | 71 | 41 | 91544 | 00294H | 20.1C | 58.8hPa | Atlas-7 |  |  |  | 190
4/28/2023 | 10:29:42 AM | CDT: | KB9SAT-13 | APLIGA,WIDE2-1,qAO,KS9A-10 | 152936 | 4034.99 | 40.3499 | 8827.95 | -88.2795 | 83 | 21 | 92800 | 00148H | 20.2C | 64.1hPa | Atlas-7 |  |  |  | 190
4/28/2023 | 10:30:42 AM | CDT: | KB9SAT-13 | APLIGA,WIDE2-1,qAR,KX9A-1 | 153036 | 4035.14 | 40.3514 | 8827.31 | -88.2731 | 74 | 32 | 94066 | 00126H | 20.6C | 89.4hPa | Atlas-7 |  |  |  | 190
4/28/2023 | 10:31:17 AM | CDT: | KB9SAT-13 | APLIGA,WIDE2-1,qAR,KE0WVG |  |  |  |  |  |  |  |  | 5.89V | 07S | 00126H | 00000000F | 0234T | 0175T | 0059T | Atlas-7
4/28/2023 | 10:31:17 AM | CDT: | KB9SAT-13 | APLIGA,WIDE2-1,qAR,W9PFD |  |  |  |  |  |  |  |  | 5.89V | 07S | 00126H | 00000000F | 0234T | 0175T | 0059T | Atlas-7 |  |  |  |  |  |  |  | [Unsupported | packet | format]
4/28/2023 | 10:31:36 AM | CDT: | KB9SAT-13 | APLIGA,WIDE2-1,qAR,K9MQ-1 |  |  |  |  |  |  |  |  | Community | High | School | IL | STEM
4/28/2023 | 10:31:36 AM | CDT: | KB9SAT-13 | APLIGA,WIDE2-1,qAR,W9PFD |  |  |  |  |  |  |  |  | Community | High | School | IL | STEM | [Unsupported | packet | format]
4/28/2023 | 10:31:56 AM | CDT: | KB9SAT-13 | APLIGA,WIDE2-1,qAR,KB0WLF-10 |  |  |  |  |  |  |  |  | Hour | - | Barry | the | Barometric | Balloon
4/28/2023 | 10:31:56 AM | CDT: | KB9SAT-13 | APLIGA,WIDE2-1,qAR,W9PFD |  |  |  |  |  |  |  |  | Hour | - | Barry | the | Barometric | Balloon | [Unsupported | packet | format]
4/28/2023 | 10:32:25 AM | CDT: | KB9SAT-13 | APLIGA,WIDE2-1,qAR,K0ATT-10 | 153219 | 4035.41 | 40.3541 | 8825.99 | -88.2599 | 79 | 42 | 96079 | 00127H | 21.2C | 121.hPa | Atlas-7 |  |  |  | 190
4/28/2023 | 10:33:25 AM | CDT: | KB9SAT-13 | APLIGA,WIDE2-1,qAR,K9MQ-1 | 153319 | 4035.55 | 40.3555 | 8825.12 | -88.2512 | 87 | 50 | 97355 | 00128H | 21.2C | 117.hPa | Atlas-7 |  |  |  | 190
4/28/2023 | 10:34:25 AM | CDT: | KB9SAT-13 | APLIGA,WIDE2-1,qAR,KE0WVG | 153419 | 4035.66 | 40.3566 | 8824.21 | -88.2421 | 90 | 35 | 98814 | 00128H | 21.2C | 117.hPa | Atlas-7 |  |  |  | 190
4/28/2023 | 10:37:25 AM | CDT: | KB9SAT-13 | APLIGA,WIDE2-1,qAR,KC8RFE-3 | 153719 | 4035.91 | 40.3591 | 8821.11 | -88.2111 | 86 | 39 | 102545 | 00129H | 21.5C | 136.hPa | Atlas-7 |  |  |  | 190
4/28/2023 | 10:38:25 AM | CDT: | KB9SAT-13 | APLIGA,WIDE2-1,qAR,KX9A-1 | 153819 | 4035.97 | 40.3597 | 8820.25 | -88.2025 | 61 | 39 | 93856 | 00129H | 21.7C | 148.hPa | Atlas-7 |  |  |  | 190
4/28/2023 | 10:39:25 AM | CDT: | KB9SAT-13 | APLIGA,WIDE2-1,qAR,KE8SZL-10 | 153919 | 4036 | 40.36 | 8819.63 | -88.1963 | 77 | 13 | 82847 | 00129H | 21.9C | 161.hPa | Atlas-7 |  |  |  | 190
4/28/2023 | 10:40:25 AM | CDT: | KB9SAT-13 | APLIGA,WIDE2-1,qAR,W9YB-1 | 154019 | 4036.08 | 40.3608 | 8819.45 | -88.1945 | 335 | 6 | 74208 | 00142H | 22.1C | 172.hPa | Atlas-7 |  |  |  | 190
4/28/2023 | 10:41:01 AM | CDT: | KB9SAT-13 | APLIGA,W9MKS-15,WIDE2*,qAR,KC6VVT |  |  |  |  |  |  |  |  | 5.91V | 06S | 00142H | 00000000F | 0246T | 0184T | 0062T | Atlas-7
4/28/2023 | 10:41:19 AM | CDT: | KB9SAT-13 | APLIGA,WIDE2-1,qAO,KS9A-10 |  |  |  |  |  |  |  |  | Community | High | School | IL | STEM
4/28/2023 | 10:41:19 AM | CDT: | KB9SAT-13 | APLIGA,WIDE2-1,qAR,W9PFD |  |  |  |  |  |  |  |  | Community | High | School | IL | STEM | [Unsupported | packet | format]
4/28/2023 | 10:41:38 AM | CDT: | KB9SAT-13 | APLIGA,WIDE2-1,qAR,KC8RFE-3 |  |  |  |  |  |  |  |  | Hour | - | Barry | the | Barometric | Balloon
4/28/2023 | 10:42:08 AM | CDT: | KB9SAT-13 | APLIGA,WIDE2-1,qAR,KX9A-1 | 154202 | 4036.19 | 40.3619 | 8819.07 | -88.1907 | 57 | 25 | 62735 | 00133H | 22.6C | 210.hPa | Atlas-7 |  |  |  | 190
4/28/2023 | 10:43:08 AM | CDT: | KB9SAT-13 | APLIGA,WIDE2-1,qAO,KS9A-10 | 154302 | 4036.18 | 40.3618 | 8818.56 | -88.1856 | 71 | 29 | 57223 | 00129H | 22.3C | 202.hPa | Atlas-7 |  |  |  | 190
4/28/2023 | 10:44:08 AM | CDT: | KB9SAT-13 | APLIGA,WIDE2-1,qAO,KS9A-10 | 154402 | 4036.39 | 40.3639 | 8817.92 | -88.1792 | 59 | 22 | 52503 | 00137H | 22.0C | 193.hPa | Atlas-7 |  |  |  | 190
4/28/2023 | 10:45:08 AM | CDT: | KB9SAT-13 | APLIGA,WIDE2-1,qAO,KS9A-10 | 154502 | 4036.6 | 40.366 | 8817.52 | -88.1752 | 48 | 18 | 48226 | 00129H | 21.6C | 183.hPa | Atlas-7 |  |  |  | 190
4/28/2023 | 10:46:08 AM | CDT: | KB9SAT-13 | APLIGA,WIDE2-1,qAO,KS9A-10 | 154602 | 4036.73 | 40.3673 | 8816.93 | -88.1693 | 52 | 37 | 44414 | 00128H | 21.3C | 177.hPa | Atlas-7 |  |  |  | 190
4/28/2023 | 10:47:08 AM | CDT: | KB9SAT-13 | APLIGA,WIDE2-1,qAO,KS9A-10 | 154702 | 4036.89 | 40.3689 | 8816.22 | -88.1622 | 84 | 33 | 40865 | 00128H | 21.1C | 177.hPa | Atlas-7 |  |  |  | 190
4/28/2023 | 10:48:08 AM | CDT: | KB9SAT-13 | APLIGA,WIDE2-1,qAR,KC8RFE-2 | 154802 | 4037.11 | 40.3711 | 8815.54 | -88.1554 | 58 | 45 | 37508 | 00127H | 20.8C | 178.hPa | Atlas-7 |  |  |  | 190
4/28/2023 | 10:49:08 AM | CDT: | KB9SAT-13 | APLIGA,WIDE2-1,qAO,KS9A-10 | 154902 | 4037.45 | 40.3745 | 8814.8 | -88.148 | 65 | 22 | 34611 | 00135H | 20.5C | 179.hPa | Atlas-7 |  |  |  | 190
4/28/2023 | 10:50:08 AM | CDT: | KB9SAT-13 | APLIGA,WIDE2-1,qAR,KC8RFE-2 | 155002 | 4037.68 | 40.3768 | 8814.38 | -88.1438 | 99 | 19 | 31841 | 00135H | 20.3C | 186.hPa | Atlas-7 |  |  |  | 190
4/28/2023 | 10:50:43 AM | CDT: | KB9SAT-13 | APLIGA,WIDE2-1,qAR,K9MQ-1 |  |  |  |  |  |  |  |  | 5.89V | 06S | 00135H | 00000000F | 0258T | 0193T | 0065T | Atlas-7
4/28/2023 | 10:50:43 AM | CDT: | KB9SAT-13 | APLIGA,WIDE2-1,qAR,W9PFD |  |  |  |  |  |  |  |  | 5.89V | 06S | 00135H | 00000000F | 0258T | 0193T | 0065T | Atlas-7 |  |  |  |  |  |  |  | [Unsupported | packet | format]
4/28/2023 | 10:51:02 AM | CDT: | KB9SAT-13 | APLIGA,WIDE2-1,qAR,KC8RFE-3 |  |  |  |  |  |  |  |  | Community | High | School | IL | STEM
4/28/2023 | 10:51:02 AM | CDT: | KB9SAT-13 | APLIGA,WIDE2-1,qAR,W9PFD |  |  |  |  |  |  |  |  | Community | High | School | IL | STEM | [Unsupported | packet | format]
4/28/2023 | 10:51:21 AM | CDT: | KB9SAT-13 | APLIGA,WIDE2-1,qAR,K9MQ-1 |  |  |  |  |  |  |  |  | Hour | - | Barry | the | Barometric | Balloon
4/28/2023 | 10:51:51 AM | CDT: | KB9SAT-13 | APLIGA,WIDE2-1,qAR,KC8RFE-2 | 155145 | 4037.91 | 40.3791 | 8813.78 | -88.1378 | 81 | 9 | 27463 | 00142H | 20.5C | 232.hPa | Atlas-7 |  |  |  | 190
4/28/2023 | 10:52:51 AM | CDT: | KB9SAT-13 | APLIGA,WIDE2-1,qAR,KX9A-1 | 155245 | 4037.99 | 40.3799 | 8813.47 | -88.1347 | 14 | 13 | 25065 | 00133H | 20.3C | 240.hPa | Atlas-7 |  |  |  | 190
4/28/2023 | 10:53:51 AM | CDT: | KB9SAT-13 | APLIGA,WIDE2-1,qAR,KC8RFE-3 | 155345 | 4038.21 | 40.3821 | 8813.37 | -88.1337 | 74 | 10 | 22677 | 00130H | 20.2C | 260.hPa | Atlas-7 |  |  |  | 190
4/28/2023 | 10:54:51 AM | CDT: | KB9SAT-13 | APLIGA,WIDE2-1,qAR,KC8RFE-2 | 155445 | 4038.26 | 40.3826 | 8813.23 | -88.1323 | 89 | 21 | 20329 | 00124H | 20.2C | 281.hPa | Atlas-7 |  |  |  | 190
4/28/2023 | 10:55:51 AM | CDT: | KB9SAT-13 | APLIGA,WIDE2-1,qAR,KX9A-1 | 155545 | 4038.12 | 40.3812 | 8812.93 | -88.1293 | 80 | 15 | 18189 | 00123H | 20.2C | 311.hPa | Atlas-7 |  |  |  | 190
4/28/2023 | 10:56:51 AM | CDT: | KB9SAT-13 | APLIGA,WIDE2-1,qAR,K9MQ-1 | 155645 | 4038.07 | 40.3807 | 8812.67 | -88.1267 | 77 | 15 | 16209 | 00123H | 20.4C | 347.hPa | Atlas-7 |  |  |  | 190
4/28/2023 | 10:57:51 AM | CDT: | KB9SAT-13 | APLIGA,WIDE2-1,qAR,KC8RFE-3 | 155745 | 4037.99 | 40.3799 | 8812.53 | -88.1253 | 183 | 6 | 14187 | 00122H | 20.6C | 389.hPa | Atlas-7 |  |  |  | 190
4/28/2023 | 10:58:53 AM | CDT: | KB9SAT-13 | APLIGA,WIDE2-1,qAR,KC8RFE-3 | 155847 | 4037.87 | 40.3787 | 8812.57 | -88.1257 | 219 | 18 | 12284 | 00121H | 21.0C | 441.hPa | Atlas-7 |  |  |  | 190
4/28/2023 | 10:59:53 AM | CDT: | KB9SAT-13 | APLIGA,WIDE2-1,qAR,KC8RFE-3 | 155947 | 4037.59 | 40.3759 | 8812.59 | -88.1259 | 221 | 9 | 10494 | 00128H | 21.6C | 500.hPa | Atlas-7 |  |  |  | 190
4/28/2023 | 11:00:53 AM | CDT: | KB9SAT-13 | APLIGA,WIDE2-1,qAR,KC8RFE-2 | 160047 | 4037.29 | 40.3729 | 8812.93 | -88.1293 | 202 | 22 | 8786 | 00167H | 22.6C | 585.hPa | Atlas-7 |  |  |  | 190
4/28/2023 | 11:01:28 AM | CDT: | KB9SAT-13 | APLIGA,WIDE2-1,qAR,KC8RFE-2 |  |  |  |  |  |  |  |  | 5.84V | 07S | 00167H | 00000000F | 0271T | 0203T | 0068T | Atlas-7
4/28/2023 | 11:01:47 AM | CDT: | KB9SAT-13 | APLIGA,WIDE2-1,qAR,KC8RFE-3 |  |  |  |  |  |  |  |  | Community | High | School | IL | STEM
4/28/2023 | 11:02:07 AM | CDT: | KB9SAT-13 | APLIGA,WIDE2-1,qAR,W9YB-1 |  |  |  |  |  |  |  |  | Hour | - | Barry | the | Barometric | Balloon
4/28/2023 | 11:02:36 AM | CDT: | KB9SAT-13 | APLIGA,WIDE2-1,qAR,KC8RFE-3 | 160230 | 4036.68 | 40.3668 | 8813.28 | -88.1328 | 190 | 9 | 6120 | 00166H | 24.0C | 709.hPa | Atlas-7 |  |  |  | 190
4/28/2023 | 11:03:36 AM | CDT: | KB9SAT-13 | APLIGA,WIDE2-1,qAR,W9IPA-11 | 160330 | 4036.54 | 40.3654 | 8813.56 | -88.1356 | 190 | 14 | 4239 | 00165H | 24.2C | 749.hPa | Atlas-7 |  |  |  | 190
4/28/2023 | 11:04:36 AM | CDT: | KB9SAT-13 | APLIGA,WIDE1-1,WIDE2-1,qAR,KC8RFE-3 | 160430 | 4036.36 | 40.3636 | 8813.66 | -88.1366 | 156 | 6 | 2570 | 00164H | 24.5C | 794.hPa | Atlas-7 |  |  |  | 190
4/28/2023 | 11:05:37 AM | CDT: | KB9SAT-13 | APLIGA,WA9RES*,WIDE2-1,qAR,KC8RFE-3 | 160530 | 4036.2 | 40.362 | 8813.54 | -88.1354 | 202 | 14 | 1304 | 00207H | 25.1C | 852.hPa | Atlas-7 |  |  |  | 190

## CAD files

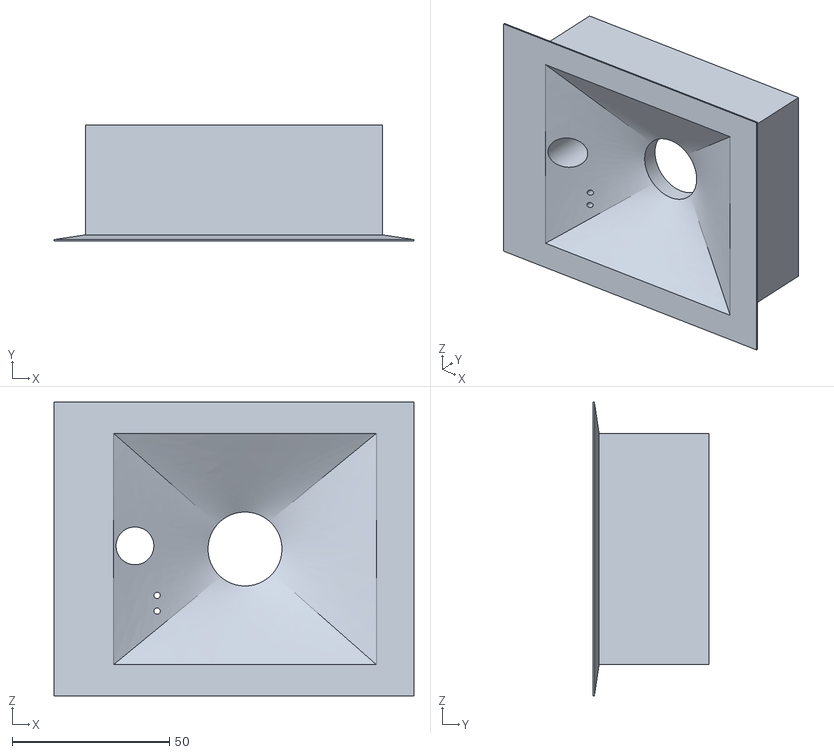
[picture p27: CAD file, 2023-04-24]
ballooninfo/3D Printed Camera Mounts/STL_cam_mounts/Akaso Mount.stl
114.5 x 37.0 x 93.5

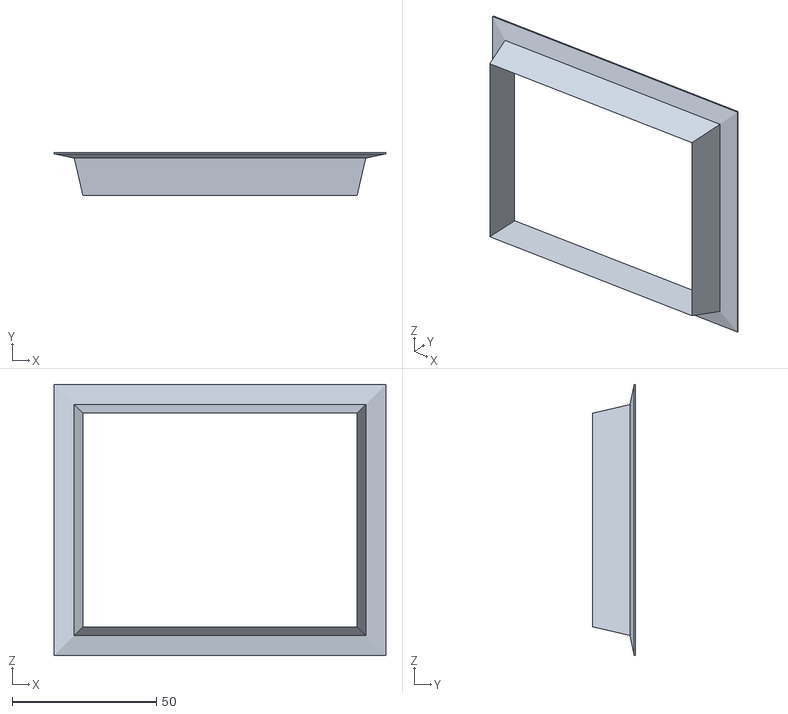
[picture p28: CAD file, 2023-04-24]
ballooninfo/3D Printed Camera Mounts/STL_cam_mounts/Akaso Mount Back.stl
114.9 x 15.0 x 93.9

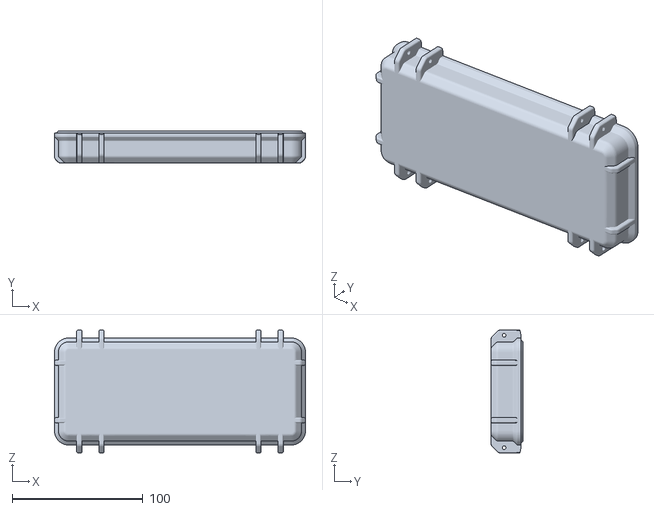
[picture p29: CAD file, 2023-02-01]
c/arduino/arduino-workbench/Frog Box Lid thin.stl
192.0 x 24.5 x 94.0

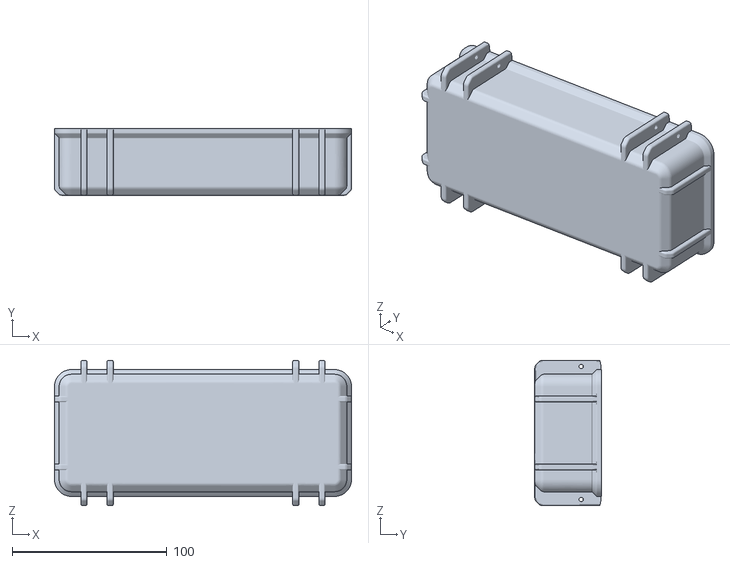
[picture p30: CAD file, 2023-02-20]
python/raspberrypico/pico-workbench/Frog Box no Seal.stl
192.0 x 43.0 x 94.0

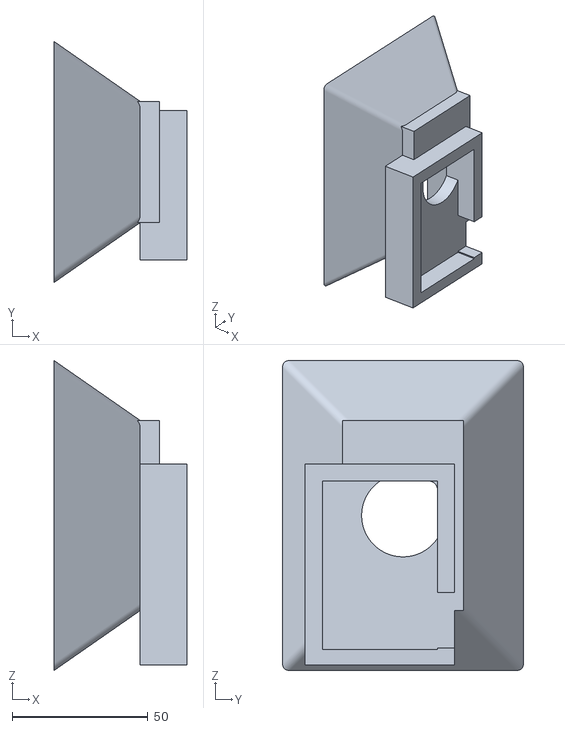
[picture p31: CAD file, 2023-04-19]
ballooninfo/3D Printed Camera Mounts/STL_cam_mounts/NEWCAMMOUNT.stl
49.0 x 88.9 x 114.3

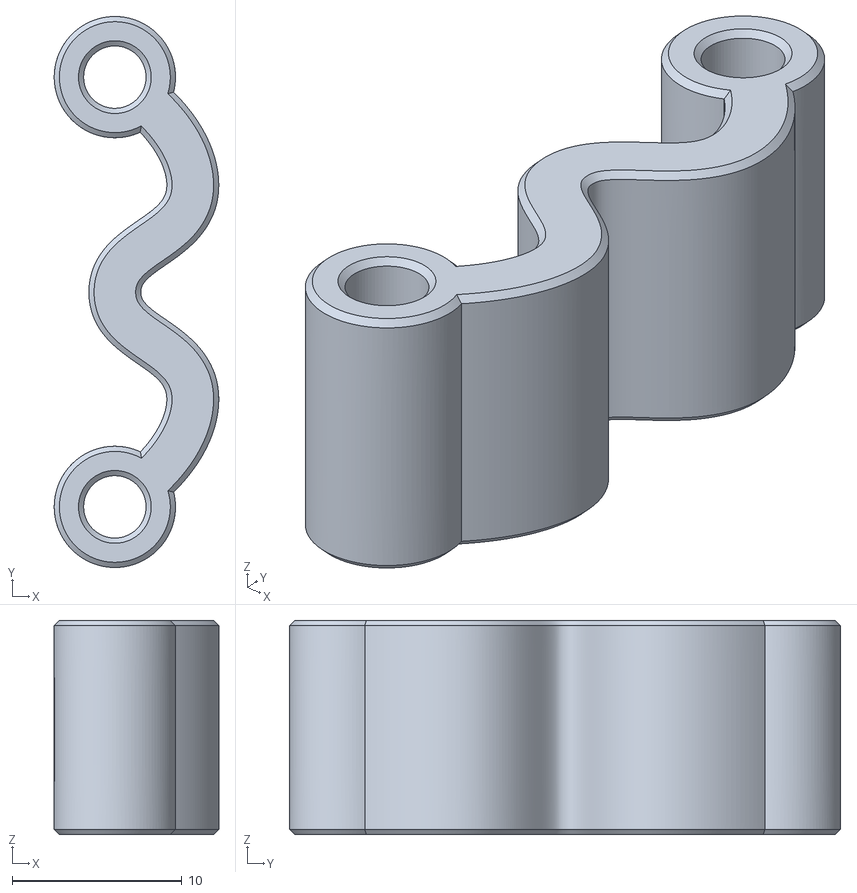
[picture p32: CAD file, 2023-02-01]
c/arduino/arduino-workbench/hinge_looser.stl
9.69 x 32.4 x 12.6

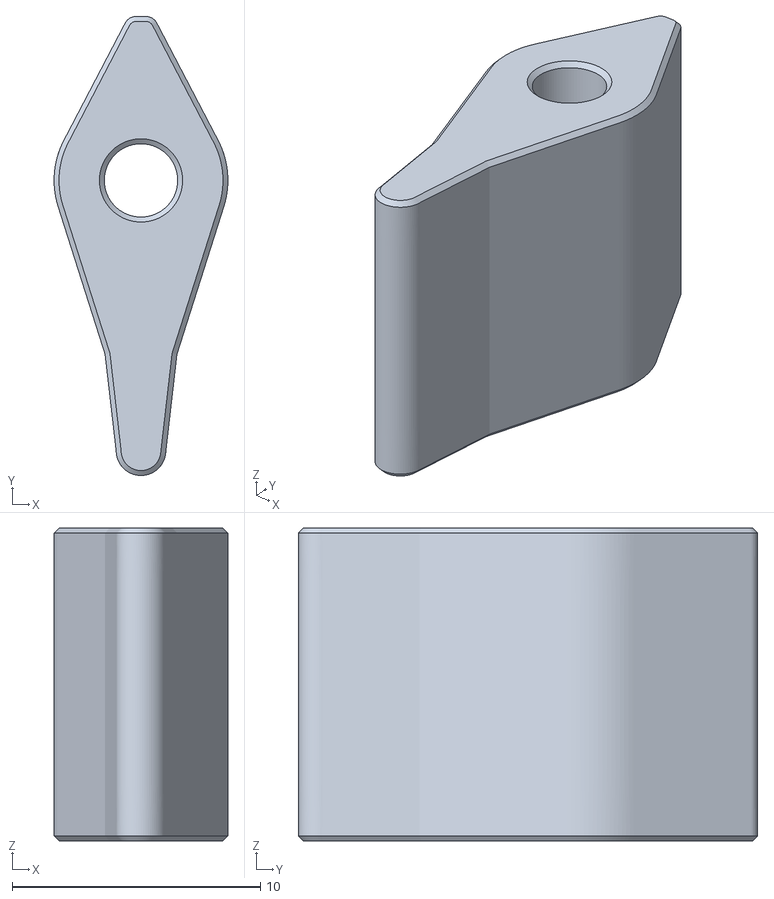
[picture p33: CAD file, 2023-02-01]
python/raspberrypico/pico-workbench/latch_cam_v2.stl
7.00 x 18.5 x 12.6

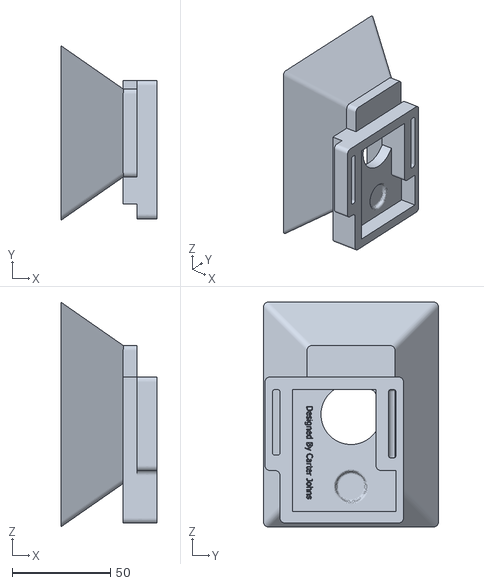
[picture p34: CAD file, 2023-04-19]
ballooninfo/3D Printed Camera Mounts/STL_cam_mounts/NEWCAMMOUNTv3.stl
49.0 x 88.9 x 114.3

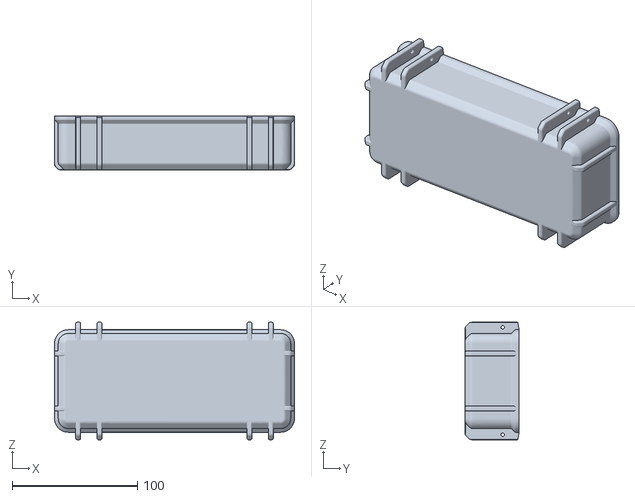
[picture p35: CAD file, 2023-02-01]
c/arduino/arduino-workbench/Frog Box no Seal - Part 1.stl
192.0 x 43.0 x 94.0

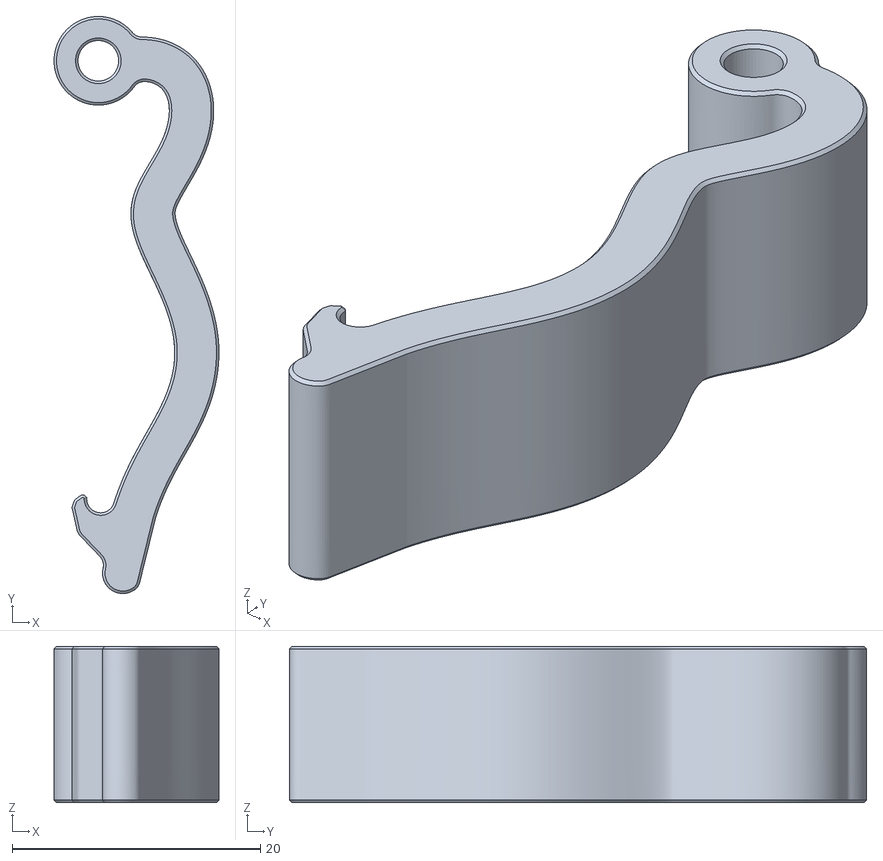
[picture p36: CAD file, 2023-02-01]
python/raspberrypico/pico-workbench/latch_arm_v2.stl
13.3 x 46.5 x 12.6

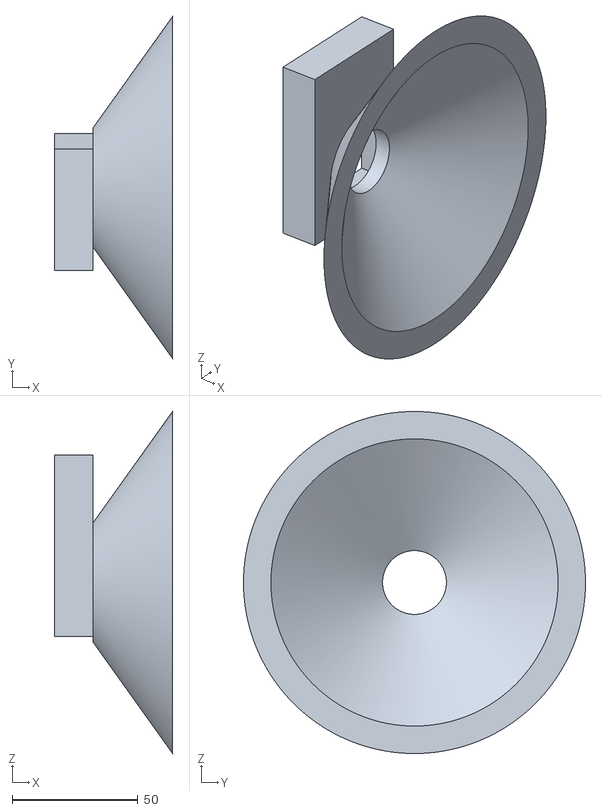
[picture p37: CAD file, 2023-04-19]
ballooninfo/3D Printed Camera Mounts/STL_cam_mounts/cam holder2.stl
47.0 x 136.1 x 136.1

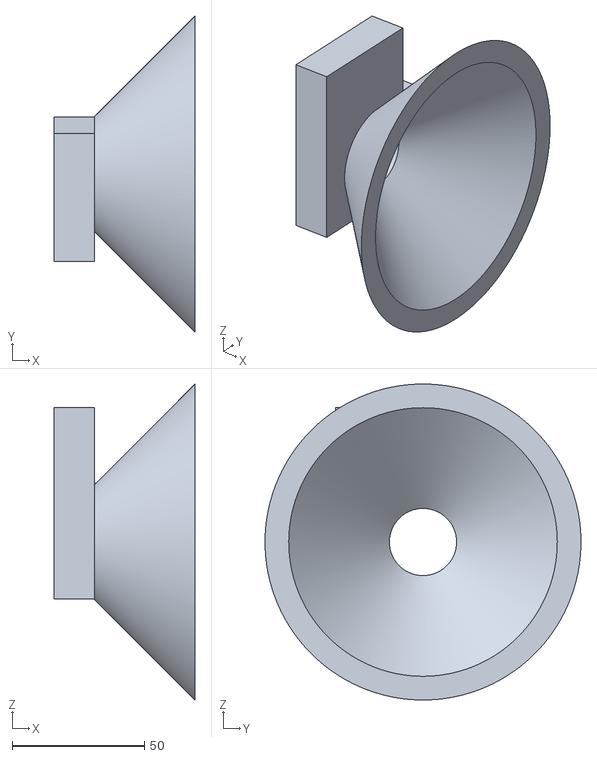
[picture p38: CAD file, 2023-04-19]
ballooninfo/3D Printed Camera Mounts/STL_cam_mounts/cam holder 1.stl
53.3 x 119.6 x 119.6

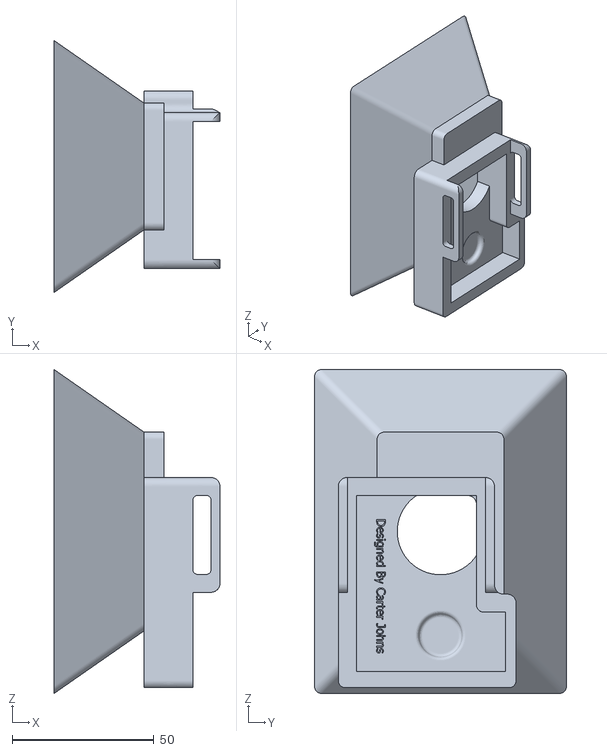
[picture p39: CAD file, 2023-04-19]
ballooninfo/3D Printed Camera Mounts/STL_cam_mounts/NEWCAMMOUNTv4.stl
58.5 x 88.9 x 114.3

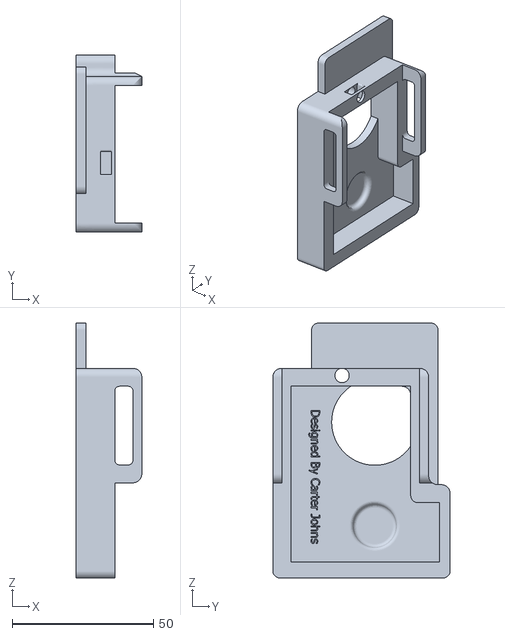
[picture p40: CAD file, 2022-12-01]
ballooninfo/3D Printed Camera Mounts/STL_cam_mounts/NEWCAMMOUNTBOTTOMHALF.stl
23.2 x 62.7 x 90.2

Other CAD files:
ballooninfo/3D Printed Camera Mounts/STL_cam_mounts/NEWCAMMOUNTv2.stl
ballooninfo/3D Printed Camera Mounts/Inventor_cam_mounts/NEWCAMMOUNTBOTTOMHALF.ipt
ballooninfo/3D Printed Camera Mounts/Inventor_cam_mounts/NEWCAMMOUNTTOPHALF.ipt
ballooninfo/3D Printed Camera Mounts/STL_cam_mounts/NEWCAMMOUNTTOPHALF.stl
c/arduino/arduino-workbench/Frog Box Lid Screws.stl
python/raspberrypico/pico-workbench/Frog Box Lid Pico Screw.stl

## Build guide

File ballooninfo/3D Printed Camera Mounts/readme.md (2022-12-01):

## 3d Printed Cam mounts

- Above in the folder called Inventor_cam_mounts there are some Inventor files that can be edited to fit other cameras
- There is also a folder called STL_cam_mounts this has the camera mounts in STL format ready to be sliced for your printer

### Assembling the cam mount
- The design uses a small chanel to align the two halves
- An M5 bolt is used with the head on the cone side, A square nut can be used in the cutout to thread the bolt into, or a nut can be placed ontop of the wall

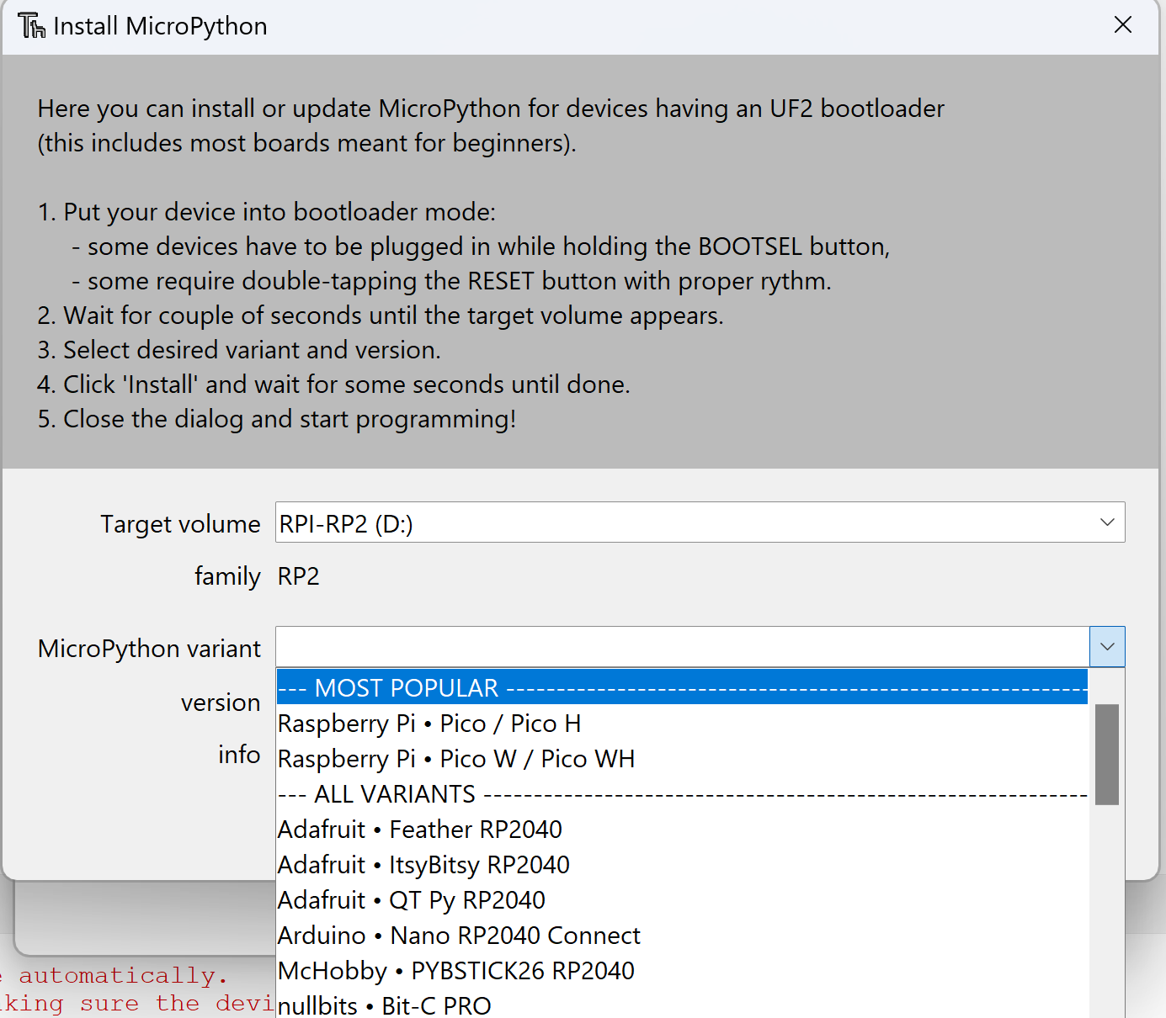
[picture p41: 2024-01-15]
python/raspberrypico/lesson-1/docs/images/thonny-install-micropython-1.png

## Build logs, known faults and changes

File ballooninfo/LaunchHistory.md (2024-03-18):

# High Altitude Balloon Launches

## 2023

|  Date |  Launch Time | Call Sign |  Code Name |  Flight Time | Max Altitude (ft) |  Flight Notes |
| --- | --- | --- | --- | --- | --- | --- |
| April 21st, 2023 | 9:26:05 CDT  | KB9LNS-13 |  Atlas-5 | 2 hours, 9 minutes and 13 seconds | 106,509 ft | Normal Community West High School IL STEM.  Balloon 1 |
| April 21st, 2023 | 9:26:05 CDT  | KB9LNS-14 |  Atlas-6 | 2 hours, 14 minutes and 49 seconds  | 85,805 ft | Normal Community West High School IL STEM.  Balloon 2; max altitude was low due to contact with latex by handler. |

## 2022

|  Date |  Launch Time | Call Sign |  Code Name |  Flight Time | Max Altitude (ft) |  Flight Notes |
| --- | --- | --- | --- | --- | --- | --- |
| April 29th, 2022 | 10:19:33 CDT | KW9D-11 |  (Atlas-3) |  3 hours, 18 minutes and 5 seconds  | 103,263 ft | GPS module lost lock after balloon popped, resulting in lack of telemetry for 11 mins |
| May 13th, 2022 | 08:46:42 CDT | KW9D-12 |  (Atlas-4) |  2 hours, 19 minutes and 38 seconds | 108,354 ft | External BME sensor failed at launch due to static discharge from cooler |

The High Altitude Balloon launch STEM program achieved its first successful flights without significant failures during this flight season.  Updated tracker code ensured the flight tracker would regularly send status message communicating it was alive, and 'fail safe' mode was incorporated.  It was with these launches the team learned the BME sensors, particularly the exterior mounted sensors, were vulnerable to static discharge from the styrofoam coolers.

Telemetry collected from these flights confirmed:
- Internal cooler temperature remained warm relative to lowest temps measures externally.  This confirmed a previous theory that the cameras generated ample heat inside the payload keeping the batteries sufficiently warm, avoiding the cutout zone starting around -30F.  The boosted confidence the cameras could be safely powered with large Lithium-ion battery packs.
- APRS flight tracker battery packs would safely power the tracker for at least one or two days on the ground.  Battery packs powering the flight trackers sending APRS telemetry data showed a drop of up to 0.25V during the flight.  Variance in the voltage was observed during the flight, with the voltage increasing briefly after launch.  This is believed to be due to the tempature changes internally or the change in impedenance load on the transmitter, but the exact reason is still unknown.
- APRS repeaters across the entire Midwest recieved and relayed telemetry packets send by the tracker.  200-300 mile diameter circle across the Midwest reaching Minnesota, Iowa, and Kansas while approaching max altitude.  The data on which repeaters recieved the packets appear to confirm the speculation the regions of highest gain radiated by the Moxon 2m antenna effectively 'projected a cone' down on earth -- the size of the cone increased as the payload attained higher altitudes.

## 2021

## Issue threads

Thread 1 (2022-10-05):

Lesson 3 (Weather Sensor): Rewrite in MicroPython

tdeknecht, 2022-10-05:
Rewriting Lesson 3 in MicroPython. Using this issue for collaboration as needed.

pankonen, 2022-10-13:
Goals:

- Have weather module wired up on the breadboard
- Working code echoing temperature, pressure, (humidity if using the bmp280)
- Code is well commented explaining whats going on to help teachers work though on their time with the class
- Run from students USB port
Bonus:
- Troubleshooting steps

gregdirst, 2022-10-16:
@pankonen  I am unable to assign tasks or push code

pankonen, 2022-10-17:
Not sure that's weird. Are you logged in? I have everyone as a maintainer I believe. It is assigned via a GitHub group but that shouldn't matter. Is anyone else having issues?

tdeknecht, 2022-10-17:
No issues here. Able to push branches and so other Issue related work.

pankonen, 2022-10-17:
Should be fixed now @gregdirst, sorry about that

gregdirst, 2022-10-23:
@pankonen I am probably doing something wrong, but I still cannot seem to do anything. I can't create a pull request and I can't add files directly. When I tried to accept that invite once I found it, it said it was 1 day past expiration (-1). Maybe I still don't have access?

pankonen, 2022-10-24:
> @pankonen I am probably doing something wrong, but I still cannot seem to do anything. I can't create a pull request and I can't add files directly. When I tried to accept that invite once I found it, it said it was 1 day past expiration (-1). Maybe I still don't have access?

Looks like you were not a member which is weird. You were the other day? I've added you, you should see the invitation.

tdeknecht, 2022-10-30:
Closed via PR https://github.com/StateFarm-STEM/hablogger/pull/13

Closed 2022-10-30.

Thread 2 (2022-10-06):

Lesson 1 (Introduction): Rewrite for Pico and MicroPython

pankonen, 2022-10-06:
Change both lesson 1's to:

Move the HAB details [here](https://github.com/StateFarm-STEM/hablogger/tree/main/ballooninfo) and focus on familiarizing teams on:
- Components
- IDE
- Electronics basics

[Java / C](https://github.com/StateFarm-STEM/hablogger/tree/main/c/arduino/lesson1)
[Python](https://github.com/StateFarm-STEM/hablogger/tree/main/python/raspberrypico/lesson1)

tdeknecht, 2022-10-12:
Hey fellas, I found the following steps and resources very quick to help me get set up with this project:

1. [Drag and Drop method for installing MicroPython on the pico](https://www.raspberrypi.com/documentation/microcontrollers/micropython.html#drag-and-drop-micropython)
2. [Set up Thonny to use the COM port for the Pico](https://core-electronics.com.au/guides/how-to-setup-a-raspberry-pi-pico-and-code-with-thonny/)

One thing to note is I'm on Windows for this. We might want to consider if users are on Mac, Ubuntu, Windows, or a Raspberry Pi when interfacing with the Pico.

Closed 2023-03-01.

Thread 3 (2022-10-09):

Weather sensor update and challenges

gregdirst, 2022-10-09:
I was unable to find a library that works for the bmp180. However, I did end up getting the BMP280 built in library working with my Adafruit BMP280. Please let me know if anyone else has had better luck with the BMP180 as that is what we were previously using.

My BMP280 does not label the pins the same as most other devices. Most devices use SDA (data) and SCL (clock). However, the Adafruit BMP280 I have uses SDI (data) and SCK (clock).
https://learn.adafruit.com/adafruit-bmp280-barometric-pressure-plus-temperature-sensor-breakout/circuitpython-test

I had to learn how I2C works using only two wires, data and clock. It also took a while to figure out that there are challenges using two devices on the same wire. I started learning I2C using the LCD 2x16 module in a kit I purchased so when I tried to add the BMP280, everything I thought I understood about connecting an I2C device no longer worked.

It wasn't until I watched a couple videos that I figured out there are 2 I2C channels (0 and 1). There are different SDA and SCL pins assigned to each one. I already placed the LCD on 0 and once I placed the BMP280 on 1 it came together.

There is more to learn about stop up resistors and how they allow multiple devices to work on the same channel.
https://www.youtube.com/watch?v=s7Lud1Gqrqw

Another challenge in general is understanding when to reboot the Pico. I still don't know exactly when I need to reboot it, but I decided to do it any time I get a runtime exception or the code breaks on a line that was previously working I click stop, reboot, then stop again, adjust the code, and run.

I also had to figure out that addressing is a critical piece (at least how I did it) to talking to a device. Care must be taken to ensure each device on a channel has a unique address. This is important when purchasing devices too.
LCD is 0x3F
BMP180 is 0x76
BMP280 is 0x77
It really helps to purchase devices that come with examples and libraries if they don't support built-in or common libraries.

I now have a working BMP280 and LCD screen displaying weather information.

gregdirst, 2022-10-09:
LCD Module
[Freenove/Freenove_LCD_Module: Apply to FNK0079 (github.com)](https://github.com/Freenove/Freenove_LCD_Module/blob/main/Freenove_LCD_Module_for_Raspberry_Pi_Pico/Python/Python_Tutorial.pdf)

gregdirst, 2022-10-09:
# ITS UGLY RIGHT NOW BECAUSE OF ALL THE TRIAL AND ERROR

# https://github.com/dafvid/micropython-bmp280

# import the required libraries
from bmp280 import *
from machine import Pin, I2C
import utime
from time import sleep
from I2C_LCD import I2CLcd

def check_devices(device_list):
    if devices == []:
        print("No i2c device !")
    else:
        print('i2c devices found:', len(device_list))

    for device in device_list:
        print("Decimal address: ", device," | Hex address: ", hex(device))

# Initiate I2C
i2c = I2C(0,           # positional argument - I2C id
          sda=Pin(4),  # named argument - serial data pin
          scl=Pin(5),  # named argument - serial clock pin
          freq=400000) # named argument - i2c frequency

# scan i2c port for available devices
devices = i2c.scan()

if devices != []:
    print("found LCD I2C address")
    check_devices(devices)
else:
    print("unable to find LCD I2C address")

lcd = I2CLcd(i2c, 0x3f, 2, 16)
lcd.move_to(0,0)
lcd.putstr("Weather Station")
lcd.move_to(0,1)
lcd.putstr("Raspberry PiPico")

# Initiate I2C
i2c = I2C(1,              # positional argument - I2C id
          sda = Pin(10),   # named argument - serial data pin
          scl = Pin(11),   # named argument - serial clock pin
          freq = 1000000) # named argument - i2c frequency

# scan i2c port for available devices
devices = i2c.scan()

if devices != []:
    print("found BMP280 I2C address")
    check_devices(devices)
else:
    print("unable to find BMP280 I2C address")

# create a BMP 280 object
#bmp280_object = BMP280(i2c_object,
#                       addr = 0x77, # change it
#                       use_case = BMP280_CASE_WEATHER)

# configure the sensor
# These configuration settings give most accurate values in my case
# tweak them according to your own requirements

bmp = BMP280(i2c, 0x77, use_case = BMP280_CASE_WEATHER)
# bmp.power_mode = BMP280_POWER_NORMAL
# bmp.oversample = BMP280_OS_HIGH
# bmp.temp_os = BMP280_TEMP_OS_8
# bmp.press_os = BMP280_TEMP_OS_4
# bmp.standby = BMP280_STANDBY_250
# bmp.iir = BMP280_IIR_FILTER_2

print("BMP Object created successfully !")
utime.sleep(2) # change it as per requirement
print("\n")

# Function for calculation altitude from pressure and temperature values
# because altitude() method is not present in the Library

def altitude_HYP(hPa , temperature):
    # Hypsometric Equation (Max Altitude < 11 Km above sea level)
    temperature = temperature
    local_pressure = hPa
    sea_level_pressure = 1013.25 # hPa
    pressure_ratio = sea_level_pressure/local_pressure # sea level pressure = 1013.25 hPa
    h = (((pressure_ratio**(1/5.257)) - 1) * temperature ) / 0.0065
    return h

# altitude from international barometric formula, given in BMP 180 datasheet
def altitude_IBF(pressure):
    local_pressure = pressure    # Unit : hPa
    sea_level_pressure = 1013.25 # Unit : hPa
    pressure_ratio = local_pressure / sea_level_pressure
    altitude = 44330*(1-(pressure_ratio**(1/5.255)))
    return altitude

#sleep(2)
#lcd.clear()
while True:
    # accquire temperature value in celcius
    temperature_c = bmp.temperature # degree celcius

    # convert celcius to kelvin
    temperature_k = temperature_c + 273.15

    # accquire pressure value
    pressure = bmp.pressure  # pascal

    # convert pascal to hectopascal (hPa)
    # 1 hPa = 100 Pa
    # Therefore 1 Pa = 0.01 hPa
    pressure_hPa = ( pressure * 0.01 ) + ERROR # hPa

    # accquire altitude values from HYPSOMETRIC formula
    h = altitude_HYP(pressure_hPa, temperature_k)

    # accquire altitude values from International Barometric Formula
    altitude = altitude_IBF(pressure_hPa)
    press = "{:.2f}".format(pressure_hPa)
    h_alti = "{:.2f}".format(h)
    i_alti = "{:.2f}".format(altitude)
    print("Temperature : ",temperature_c," Degree Celcius")
    print("Pressure : ",pressure," Pascal (Pa)")
    print("Pressure : ",press," hectopascal (hPa) or millibar (mb)")
    print("Altitude (Hypsometric Formula) : ", h_alti ," meter")
    print("Altitude (International Barometric Formula) : ", i_alti ," meter")
    print("\n")
    #utime.sleep(1.5)

    lcd.move_to(0,0)
    lcd.putstr("Pico Weather Stn")
    lcd.move_to(0,1)
    lcd.putstr("                ")
    lcd.move_to(0,1)
    lcd.putstr("Temp: ")
    lcd.putstr(str(temperature_c))
    lcd.putstr(" C")
    sleep(1.5)
    lcd.move_to(0,1)
    lcd.putstr("                ")
    lcd.move_to(0,1)
    lcd.putstr("Press:")
    lcd.putstr(str (press))
    lcd.putstr(" hPa")
    sleep(1.5)
    lcd.move_to(0,1)
    lcd.putstr("                ")
    lcd.move_to(0,1)
    lcd.putstr("Alt: ")
    lcd.putstr(str (i_alti))
    lcd.putstr(" mtr")
    sleep(1.5)

pankonen, 2022-10-12:
Hey @tdeknecht have a look at Greg's notes. @gregdirst Tyler picked up the BMP section when we met.

tdeknecht, 2022-10-12:
@gregdirst , these findings and code provided relate to https://github.com/StateFarm-STEM/hablogger/issues/1. I suggest opening a pull request for that lesson if this is all working for the BMP280. That still leaves us with the BMP180, which might be preferred...? A decision needs to be made around which sensor we want to use given what you've found so far.

gregdirst, 2022-10-16:
I have a branch on my machine after cloning the repo. Do I need to undo that and do a pull request instead? I am new at this Git stuff. I can only do simple things.

pankonen, 2022-10-17:
Greg, I'm sorry I didn't finish clicking through the prompts when I added you to the repo. You should be able to accept the invitation and be good to go.

pankonen, 2022-10-17:
I haven't (I should though) enabled merge approvals etc. yet. You can clone, make changes, push, commit, and merge. I have been using the desktop client on my Mac and honestly have t paid close attention to the details. That said it works really nice! Also, side note, if you install the GitHub app on your phone it will use that for mfa which is nice.

tdeknecht, 2022-10-17:
> Ok, thanks @pankonen. However, after seeing the pull requests, I think I am doing it wrong the way I created my branch and want to push my changes up. Do I create a pull request? I haven't done them before.

You create a branch locally, make changes, push the branch up. That branch is something you work on, but other can collaborate if they decide to pull your branch local. Each time you make changes, follow  normal commit process and push your branch up. Sometimes you might have to sync up with `main` so you aren't behind `main` with any commits. When you are ready to merge your changes into `main`, open a Pull Request. Someone else will review the Pull Request, approve it, then you can merge it into `main`.

Functionally it's about the same as how GitLab works.

gregdirst, 2022-10-25:
Sorry for being a pain and is very discouraging, but I have a branch named greg and I can pull, but cannot push. Here is what I get...

gregd@DESKTOP-M2BBE31 MINGW64 /F/Dev/git/hablogger/python/raspberrypico/lesson3 (greg)
$ git push --set-upstream origin greg
Enter passphrase for key '/f/Users/gregd/.ssh/id_rsa':
ERROR: Permission to StateFarm-STEM/hablogger.git denied to gregdirst.
fatal: Could not read from remote repository.

Please make sure you have the correct access rights
and the repository exists

tdeknecht, 2022-10-26:
@gregdirst try setting your remote to pulling over HTTPS instead of SSH. Do a `git remote set-url origin https://github.com/StateFarm-STEM/hablogger.git` in the project, then try pushing again.

tdeknecht, 2022-10-30:
Closed via PI https://github.com/StateFarm-STEM/hablogger/pull/13

Closed 2022-10-30.

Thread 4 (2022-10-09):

GPS update

gregdirst, 2022-10-09:
I have a working GPS module, but it uses UART connection to work and I want to do I2C. I will need to learn the master/slave concept because I already have an LCD module and a BMP280 using both I2C channels.

This is setup by itself on a second Pico I have and does not use the LCD.

gregdirst, 2022-10-09:
from machine import Pin, UART, I2C
#from ssd1306 import SSD1306_I2C

import utime, time

#i2c=I2C(0,sda=Pin(0), scl=Pin(1), freq=400000)
#oled = SSD1306_I2C(128, 64, i2c)

gpsModule = UART(1, baudrate=9600, tx=Pin(4), rx=Pin(5))
print(gpsModule)

buff = bytearray(255)

TIMEOUT = False
FIX_STATUS = False

latitude = ""
longitude = ""
satellites = ""
GPStime = ""

def getGPS(gpsModule):
    global FIX_STATUS, TIMEOUT, latitude, longitude, satellites, GPStime

    timeout = time.time() + 8
    while True:
        gpsModule.readline()
        buff = str(gpsModule.readline())
        parts = buff.split(',')

        if (parts[0] == "b'$GPGGA" and len(parts) == 15):
            if(parts[1] and parts[2] and parts[3] and parts[4] and parts[5] and parts[6] and parts[7]):
                print(buff)
        
                try:
                    latitude = convertToDegree(parts[2])
                except:
                    latitude = parts[2]
        
                if (parts[3] == 'S'):
                    latitude = '-' + latitude
        
                try:
                    longitude = convertToDegree(parts[4])
                except:
                    longitude = parts[4]
            
                if (parts[5] == 'W'):
                    longitude = '-' + longitude
            
                satellites = parts[7]
                GPStime = parts[1][0:2] + ":" + parts[1][2:4] + ":" + parts[1][4:6]
                FIX_STATUS = True
                break
        
        if (time.time() > timeout):
            TIMEOUT = True
            break
        utime.sleep_ms(500)

def convertToDegree(RawDegrees):

    RawAsFloat = float(RawDegrees)
    firstdigits = int(RawAsFloat/100)
    nexttwodigits = RawAsFloat - float(firstdigits*100)

    Converted = float(firstdigits + nexttwodigits/60.0)
    Converted = '{0:.6f}'.format(Converted)
    return str(Converted)

while True:

    getGPS(gpsModule)

    if(FIX_STATUS == True):
        print("Printing GPS data...")
        print(" ")
        print("Latitude: "+latitude)
        print("Longitude: "+longitude)
        print("Satellites: " +satellites)
        print("Time: "+GPStime)
        print("----------------------")

#         oled.fill(0)
#         oled.text("Lat: "+latitude, 0, 0)
#         oled.text("Lng: "+longitude, 0, 10)
#         oled.text("Satellites: "+satellites, 0, 20)
#         oled.text("Time: "+GPStime, 0, 30)
#         oled.show()

        FIX_STATUS = False

    if(TIMEOUT == True):
        print("No GPS data is found.")
        TIMEOUT = False

tdeknecht, 2022-11-20:
I re-wrote the GPS code as a driver and merged it in PR https://github.com/StateFarm-STEM/hablogger/pull/14

Closed 2022-11-20.

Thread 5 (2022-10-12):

IDE / development environment decision

pankonen, 2022-10-12:
While poking around the other day I found there are what looks like two options for working with the Pico.

[Thonny](https://thonny.org/)

- More like a default Python SDK from what I can tell?

[Circuit Python](https://circuitpython.org/)

- Looks to ease the introduction to Python

What are everyones thoughts?

tdeknecht, 2022-10-12:
These are two different things and can be treated as separate decisions.

Thonny is the IDE or code executor we'd be using to interface with the Pico. You can choose within Thonny CircuitPython as an interpreter the same way you can choose MicroPython.

For the interpreter we could go the route of MicroPython or CircuitPython. Being inexperienced at this point, my vote is for MicroPython because we've not yet hit any limitations with the packages it comes with. If we hit scenarios where MicroPython isn't cutting it and we don't want to compile our own interpreter, we could look closer at CircuitPython.

All that said, I vote Thonny using MicroPython to start.

pankonen, 2022-10-13:
For the time being lets move forward with Thonny

Closed 2022-10-17.

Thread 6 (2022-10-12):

Lesson 2 (Blinking Lights): Rewrite in MicroPython

tdeknecht, 2022-10-12:
Rewrite [Lesson 2 from pyinthesky project](https://github.com/StateFarm-STEM/pyinthesky/tree/main/lesson2) using MicroPython.

tdeknecht, 2022-10-12:
@jessebaird , while tinkering from a learning standpoint, I was able to get the onboard LED to blink using this snippet:

```python
# Blinks onboard LED every 1 second

from machine import Pin
import time

led = Pin(25, Pin.OUT)

while True:
    led.toggle()
    time.sleep(1)
```

pankonen, 2022-10-13:
Goals:

- Have LED's wired up on the breadboard 9they will need a resistor inline with each LED)
- Working code:
  - Flash each LED
  - Use variables to set time on
  - Use variable for pause between flashes
- Code is well commented explaining whats going on to help teachers work though on their time with the class
- Run from students USB port

Bonus:
- Troubleshooting steps

jessebaird, 2022-10-25:
Also, since this is the first lesson, should I include how-tos on installing Micropython/Thonny or will this all be set up for them ahead of time?

jessebaird, 2022-10-25:
One other question.  Will the kits that the students have include a breadboard?

pankonen, 2022-10-27:
> @pankonen One other question. Will the kits that the students have include a breadboard?

yup, they will all have a kit with resistors, leds's, wires, breadboards, etc

jessebaird, 2022-10-29:
I uploaded the files for various blinking LED options.  I will work on the instructions with pictures next.

jessebaird, 2022-11-05:
I have completed the final draft of lesson 2, ready for review.  I'm happy to make tweaks as needed.

https://github.com/StateFarm-STEM/hablogger/tree/main/python/raspberrypico/lesson2

Closed 2022-11-05.

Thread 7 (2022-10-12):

Lesson 4 (GPS Sensor): Rewrite in MicroPython

tdeknecht, 2022-10-12:
Rewrite [lesson 4 from pyinthesky](https://github.com/StateFarm-STEM/pyinthesky/tree/main/lesson4) in MicroPython with compatibility with the Pico

pankonen, 2022-10-13:
Goals:

- Have GPS module wired up on the breadboard
- Working code echoing latitude, longitude, time
- Code is well commented explaining whats going on to help teachers work though on their time with the class
- Run from students USB port
Bonus:
- Troubleshooting steps

tdeknecht, 2022-11-20:
Lesson 4 completed in this PR: https://github.com/StateFarm-STEM/hablogger/pull/14

Closed 2022-11-20.

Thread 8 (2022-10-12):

Lesson 5 (SD Card Storage): Rewrite in MicroPython

tdeknecht, 2022-10-12:
Rewrite [lesson 5 from pyinthesky project](https://github.com/StateFarm-STEM/pyinthesky/tree/main/lesson5) using MicroPython and Pico compatibility

pankonen, 2022-10-13:
Goals:

- Have SD card module wired up on the breadboard
- Working code writing / appending the CSV file every 30 seconds
- initialize the SD card, write a file, append to the file, close the SD card after each write
  - CSV file format is not important it can be random. When we do lesson 6 it will follow this format
    - temp, humidity, pressure, lat, long, alt, time
- Code is well commented explaining whats going on to help teachers work though on their time with the class
- Run from students USB port
Bonus:
- Troubleshooting steps

tdeknecht, 2022-10-21:
@pankonen , what are the data formats for the following values (int, string, float, etc.)?

temp, humidity, pressure, lat, long, alt, time

tdeknecht, 2022-10-22:
Implemented via https://github.com/StateFarm-STEM/hablogger/pull/12

pankonen, 2022-10-22:
Temp two decimal places, humidity two decimal places, humidity two decimal places, lat 4 decimal places, long 4 decimal places, altitude two decimal places, time hh:mm:ss

Closed 2022-10-22.

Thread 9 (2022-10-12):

Lesson 6 (All Together): Rewrite in MicroPython

tdeknecht, 2022-10-12:
Rewrite [lesson 6 in pyinthesky project](https://github.com/StateFarm-STEM/pyinthesky/tree/main/lesson6) in MicroPython with Pico compatibility

pankonen, 2022-10-13:
Goals:

- Have all components wired up on the breadboard
  - Weather sensor, GPS, SD card
- Working code with enabling all sensors writing / appending the CSV file every 30 seconds
  - CSV file format:
    - temp, humidity, pressure, lat, long, alt, time
- Code is well commented explaining whats going on to help teachers work though on their time with the class
- Run from a battery like we would when we fly

tdeknecht, 2022-11-22:
Lesson 6 added in PR https://github.com/StateFarm-STEM/hablogger/pull/15

Closed 2022-11-22.

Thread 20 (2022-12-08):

Display module to see a system check and know the logger is working correctly

pankonen, 2022-12-08:
We need a method to see if the HABlogger is working properly when flying. We will not be able to see console output in the field when we are loading the payload.

I have a pack of these [I2C OLED Display Modules](https://smile.amazon.com/gp/product/B08VNNCLHD/ref=ppx_yo_dt_b_search_asin_title?ie=UTF8&th=1) we can test. I have sent some to the AZ crew for development. I will drop some by Trevor, Tyler, Jesse, etc this weekend.

We need to see that each device is working as expected:
- BMP is logging accurate data
- GPS is logging accurate data
- SD card is able to be written
  - Is it possible to see if data is written to the card

tdeknecht, 2022-12-29:
Implemented via https://github.com/StateFarm-STEM/hablogger/pull/22

tdeknecht, 2023-01-24:
Closed via https://github.com/StateFarm-STEM/hablogger/pull/22

Closed 2023-01-24.

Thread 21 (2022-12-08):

GIT process / procedures for classes

pankonen, 2022-12-08:
Determine best way to manage Git resources for each class

- Should they Fork / Clone
- How do they get updates when we modify the HABlogger repo
- Issues / discussions
- Anything else?

snarfattack, 2022-12-08:
I've been thinking about this, especially for the c version of pico that I'm working on because there is a lot of framework they will need to clone to get going. Having all the projects in a single repo is not ideal. I'm expecting that a separate repo will be ideal for the c code framework to make the setup process easier.

Other than that base framework, If the students doing the same thing we were last friday, visiting a web page to follow lesson instructions, copying a pasting a section of code into an IDE, I don't think there is a need for them to fork or clone the lesson repo. They would get updates when they refresh the web page/site.

tdeknecht, 2022-12-10:
@snarfattack I'm taking a similar approach in the Python project, if I'm following your thoughts correctly. There are _drivers_ that simplify interfacing with peripheral modules. They simplify the code for students, making it more about configuring pins and reading/writing data than getting into the complexities of interfacing a module with the Pi Pico.

In my case I'm creating a `/drivers` folder with a driver for each module (GPS, SD Card, Atmospheric). I'm adding a step to Lesson 1 on how to install drivers to the Pi Pico.

pankonen, 2022-12-27:
Thanks fellas. I was going to ask the same question about what dependencies they would need for either C or Python versions.

I want to keep the lessons / project in one repo where possible for now anyways. We have some issues with Git if the students need to login due to a law in Illinois to "protect" students. I have not followed up since the spring semester but at the time they were not able to create logins through school until the site was "approved". I assume if a repo was public they could clone without logging in but could not fork or do any activities requiring a login / authentication. I will ping the teachers and see where this is at.

My thoughts were more along project management and issue management with each class. for this semester I think we will proceed with what we have and also offer a GitLab internally for mentors / lead mentors to comment where the students and teachers cannot see. I'm going to be pushing soon to expand this program to more schools and more locations like our hubs etc. and I think we may need to figure how to handle support etc.

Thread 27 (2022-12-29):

Project Workbench prototyping

pankonen, 2022-12-29:
We have been working on a design to contain the components, protect them from static, and ruggedize the project a bit.

[Project Workbench](https://github.com/StateFarm-STEM/hablogger/tree/main/project_workbench)

-	We need to add standoffs for each component. We only have the microcontrollers as I was out of kits with the original parts to give Carter for design
-	We need to modify the sd card compartment to allow the sd card to be removed and replaced by student when they do the labs and need to check data
-	We need to modify the cable wrap holders in the cable compartment, raise them up a bit for access
-	We are trying to determine how to latch it. Some ideas are being tested. Worse case we can use a latch from the hardware store.

Please provide feedback!

tdeknecht, 2022-12-29:
How confident are we in the connections we'll be wiring up between the Pico and the modules? In other words, should we have a more permanent solution we use with confidence, potentially printing PCBs from a site like www.4pcb.com?

For the students we'll want them to wire things up and not have things permanently set (or have to deal with soldering/de-soldering). I think it'd be cool to have a couple rock-solid setups though to prove out our design overall.

snarfattack, 2022-12-29:
I would recommend using the frog box style to start from and then divide it
up into part and item storage.

https://www.thingiverse.com/thing:4094861

On Thu, Dec 29, 2022, 10:09 AM Tom Pankonen ***@***.***>
wrote:

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

pankonen, 2023-02-01:
Going to print one here when I get a break in meetings! I just approved and merged your pull request Josh, thank you!

pankonen, 2023-02-28:
These are complete! I've printed all of them for the student groups and will be assembling. I'm hoping the students will be using them Friday!

pankonen, 2023-03-15:
Nicely done @snarfattack! Printed, assembled and delivered... almost. Kevin will be dropping normal west tomorrow.

Closed 2023-03-15.

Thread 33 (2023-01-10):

Library for SD Card

feeneyai, 2023-01-10:
I don't see which specific libary we should use for the SD Card Module

tdeknecht, 2023-01-10:
Is this issue related to the Python code or C code?

If Python, I am using the driver located here: https://github.com/StateFarm-STEM/hablogger/blob/main/python/raspberrypico/drivers/src/sdcard.py

I pulled the driver local to the project to keep functionality consistent, and to avoid confusion with the instructors about which driver version to use from the open source project.

feeneyai, 2023-01-11:
The C Code.  It says "using the SID library" in the lesson but when I go through Arduino's Library Manager to bring in the library there are some choices so I am not sure which to select.

pankonen, 2023-02-01:
Hey @gregdirst can you have a look?

gregdirst, 2023-02-28:
Can you provide a link to where you are seeing "using the SID library"

gregdirst, 2023-02-28:
@feeneyai I think if you just add this to the top of your code it will know what you need...

```
#include <SPI.h>
#include <SD.h>
```

pankonen, 2023-03-15:
I'm going to say this is fine as we completed the lesson last week and I ran through it at home with no issues with the fat client.

Closed 2023-03-15.

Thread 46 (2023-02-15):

Lesson 3 - Suggestions

wardmr, 2023-02-15:
Hi there hablogger team. Thanks for all the work you have done with this. I just went through the raspberrypico lesson 3 and had some suggestions:

- Installing the driver was a little tricky and may create a lot of issues for students especially step 3. It may be my version or settings but stopping/refreshing did not make my raspberry pico folders show up on the left navigation.
- Once stopping/refreshing and then clicking file>open, I then had the option of opening from computer or the raspberry pico. Clicking the raspberry pico pulls up a window that when right clicked gives the option for creating the new directory "drivers".
- Then when trying to save bmp180.py to pico, it does not give the option to save to computer or pico. Stopping/refreshing gave the option to open from the bmp180.py from the computer then stopping/refreshing again gave me the option to save the bmp180.py to the raspberry pico. I did it two different ways (in case students have more issues):
- Opening bmp180.py from computer and saving it to pico
- Copying and pasting the driver code into a new thonny file then saving to pico

I have a feeling if students solve this issue (or never have it) the lesson may be fairly quick. One thing that may be cool to add is an extra activity once they getting the readings here are my ideas:
-Students could concatenate the unit of measure to the end of the readings (rather than displayed at the front)
-Students could create a function inside the main entry point that will take in a measurement in meters and will return a value in feet (I know, imperial is gross but it could be a good exercise for students). Students can then call this function in the print statement on line 29 and pass through "altitude". Students should be able to figure this out eventually, but it has been about 6 months since they have seen functions in Python. Mentors/I can guide groups with this.

Sorry for the long issue... Hope it makes sense!

Note: I did it with a raspberry pico W

TrevBart, 2023-02-15:
This is good feedback. I will add more to the steps to strengthen the driver installation.

I also like the stretch goals at the end as well. I will add some "things to try" at the bottom above the video walk-through.

Thank you!

tdeknecht, 2023-02-15:
@TrevBart i use similar driver install steps in other lessons. We might be able to come up with something repeatable across all these lessons.

feeneyai, 2023-02-15:
Hi Trevor, thank you for all you are doing!  This was something I was working on as well for Friday.  In the Arduino lesson the altitude is not written to the Serial Monitor so I thought it would be good to have the students do that.  You certainly don't have to include this but I wanted to have the students do a little more.  I think some will finish the lesson early so I was trying to think of something else they could do with this sensor.

Extension - Lesson 3 - What is our Altitude?

In this extension you are going to measure our altitude and report it in the serial monitor.

You should have successfully wired the BMP_180 sensor to record the temperature in degrees Fahrenheit and the Barometric Pressure in inches of mercury (HG) to the Serial Monitor.

What was the raw data from the BMP_180 for each of those?

Did you cup your hands around the sensor and watch the temperature rise? Don't grab the sensor or press on it, gently cup your hands around it and it shouldn't take long to raise the temperature.

The BMP_180 also measures Altitude!  Add the appropriate code to capture the altitude and record the altitude in the Serial Monitor. Output the altitude after the other two measurements.  Look up to see what that number means.  Label the output appropriately. Just as the temperature was changed to a more common measure in the United States, change the Altitude to a more common measure in the United States.  Label the output appropriately.

Raise your system, does the altitude change?

Look up to see what that number means and label the output appropriately.

What is the range of values for the altitude?

Is the BMP_180 a good sensor for tracking a weather balloon for altitude?

You may want to slow down the output so it can be read more easily.

wardmr, 2023-02-15:
I believe if I had view>files turned on before stopping/refreshing this could solve the problem I had.

TrevBart, 2023-02-16:
This was great. I added sections on altitude for the Arduino and cleaned up the BMP library section. I have added more progress checks in the Python driver sections as well. I love thought starters and discussion so I added a "Want More" section to have the students try/think about/validate their understanding. I think it would be good to continue this in the next lessons as well. Please keep this feedback coming!

Closed 2023-02-16.

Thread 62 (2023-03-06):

Lesson update for Python labs

pankonen, 2023-03-06:
Guidance for troubleshooting thonny connection issues

- Check ports
- Ensure software is pushed to the Pico for initial startup (c or python version)
  - Instructions

tdeknecht, 2023-12-26:
This issue is being address systematically through updates to each Python lesson when challenges are added. The existing Troubleshooting section in each lesson covers some cases, and more troubleshooting examples are being added as they are uncovered.

Closed 2023-12-26.

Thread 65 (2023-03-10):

Lesson 5 image has differences for some devices

snarfattack, 2023-03-10:
https://github.com/StateFarm-STEM/hablogger/blob/main/python/raspberrypico/lesson-5/docs/pi-pico-hw150.png

The devices we have in class are marked as MOSO, not MISO for the pin.

snarfattack, 2023-03-10:
Also, the picture is reversed from the pin order on the device.

pankonen, 2023-03-10:
oops should have seen your issue first. I opened one with the same thing and some other additions related to that :)

snarfattack, 2023-03-10:
hahah, Was just going to relate them!

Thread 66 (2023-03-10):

Lesson 5 - link to main.py is 404

snarfattack, 2023-03-10:
This points to the wrong location:
[./src/lesson5/main.py](https://github.com/StateFarm-STEM/hablogger/blob/main/python/raspberrypico/lesson-5/src/lesson5/main.py).

Should be
[./src/main.py](https://github.com/StateFarm-STEM/hablogger/blob/main/python/raspberrypico/lesson-5/src/main.py).

pankonen, 2023-03-10:
Fixed

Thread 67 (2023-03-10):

Lesson 6 Additional detail needed

snarfattack, 2023-03-10:
No need to move the pico over in the breadboard!

Link 5v from the pico pin 1 to the +(Red) bus on the breadboard. Link GND from the pico pin3 to the -(Blue). Then each sensor board, connect the VCC to the +(Red) bus and the GND to the -(Blue) bus.

We need to enhance the instructions to include a link to the new main.py.

Main.py includes a reference to SSD1306 for the OLED, which hasn't been covered yet, and isn't actually used in the main.py.

tdeknecht, 2023-03-13:
@snarfattack I removed the SSD1306 import (it was left over from when I had the OLED in this lesson). I also removed the LED code to keep things simpler.

I follow what you are saying about using the breadboard. I did not have the pinout added in the diagram for the breadboard, assuming at this point the students would be able to infer from the wiring diagram the best way to use the breadboard for all the modules. In a way, leaving somewhat of a challenge for them to figure out that bit of the wiring. I did add a hint to using the breadboard based on how I have it wired and because of your suggestion.

Can you expand on what you mean by the "new main.py?"

You can see my current changes in [this branch](https://github.com/StateFarm-STEM/hablogger/tree/issue-67). Feel free to add comments in the code.

snarfattack, 2023-03-13:
In class, couple of our teams started by attempting to remove the pico from the breadboard to shift it over to get more holes to the side of the 5v and gnd pins. Since lessons 3-5 didn't re-inforce the concept of how to use the power bus, they forgot it. I had to re-teach it to our teams. Worried that people might damage picos if we leave it up to them and they decide to move picos.

I see it includes a link to the main.py now, but the path is wrong and returns 404 as there is a duplicate lesson 6 in the path.

Thanks!

tdeknecht, 2023-03-13:
@snarfattack I see what you mean about not wanting to remove the pico. If I get time between now and Friday I'll see about including a breadboard in the pinout diagram to use the power buses on the sides.

I updated the link, too. Nice catch!

tdeknecht, 2023-03-14:
@snarfattack I pulled in @TrevBart fixes and pushed the branch. I'm going to merge it. This should close out this issue.

@TrevBart , I removed the `time.sleep(1)` you included. I've seen that mess with the GPS data collection before. I don't want to inadvertently add an issue for the students.

tdeknecht, 2023-03-15:
Issues fixed in https://github.com/StateFarm-STEM/hablogger/pull/71

Closed 2023-03-15.

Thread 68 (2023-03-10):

Need to account for Pico and Pico W pin differences

pankonen, 2023-03-10:
We need to update the labs to show both pico and pico w's
- Wiring differences
- Pics (Maybe standardize like Tylers awesome pic and diagrams)
- How to ID which one your working with

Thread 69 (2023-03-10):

Add text to labs to follow labels on the components

pankonen, 2023-03-10:
We found some SD boards are different than the pics in lab 5
- Update ALL labs to have verbiage about following the labels on the device
- Add a tip to take a pic for reference as its hard or impossible to see once plugged in the bread board (example GPS)
- Add notes to ALWAYS triple check wiring is correct before plugging in the USB cable on all labs (we had students in a couple groups wire the SD module wrong which caused it to heat up)

tdeknecht, 2023-10-26:
This is a duplicate of issue https://github.com/StateFarm-STEM/hablogger/issues/65.

Closed 2023-10-26.

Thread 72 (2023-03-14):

Lesson 1 - order of install GIT and VSCode

SeanSchick, 2023-03-14:
The way it's laid out in lesson one you install VS Code after Git. But for the Git installer to use VS Code as the default editor, it needs to have VS Code there first. Otherwise Git won't let you select and continue the install

pankonen, 2023-03-15:
Which lesson 1? i don't see either installing Git or VS Code?

snarfattack, 2023-03-15:
This is in the c/pico version. Makes perfect sense.

As a reminder to myself, Tom found a new bundle from pi to setup the environment. So I need to review that too.

pankonen, 2023-03-15:
> As a reminder to myself, Tom found a new bundle from pi to setup the environment. So I need to review that too.
https://www.raspberrypi.com/news/raspberry-pi-pico-windows-installer/

tdeknecht, 2024-01-13:
I don't see VScode referenced in either Lesson 1 for either Arduino or Pico. It's possible this has been corrected via other lesson adjustments. Any thoughts before I close this down, @snarfattack @pankonen @TrevBart ?

pankonen, 2024-01-15:
We can close this. Things have changed with how the pico works inside tooling. @snarfattack found we can run things as is on pico through Arduino studio and I think Thonny which wasn't the case before. Let's code this and address future work porting to Pico in other issues.

Closed 2024-01-15.

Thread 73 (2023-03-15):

Lesson 6

feeneyai, 2023-03-15:
These suggestions could be part of the Troubleshooting section.

It would be good to remind the students of the three libraries in case they use a classroom laptop in which the libraries were not previously installed.  Or at least prompt them to look in the previous lessons to make sure they have all three libraries installed in the Arduino software.

If a student writes a file to the SD card (so it ran successfully) and they want to make changes and run again, it may be good to remind students that they need to delete the .txt file written to the SD card if they want to run it again.

After I had everything connected and software running, one of the things that I experienced was not knowing if things were working while I was waiting for signal from the GPS sensor. There are the three initialization statements but nothing is output or written to the SD card or Serial Monitor unless the GPS sensor is actively acquiring a signal.  Another suggestion to Want More? would be to have the students print key things to the Serial Monitor so they can see progress. This does not write to the SD card but would help with monitoring progress. Suggestions "Temperature is " then temp, so they know it is operating while they wait to get GPS signal - it also would change while they walked around trying to get the GPS signal.  They could also add appropriate output statements like GPS Working - Satellites Not Found, GPS Working - Satellites found.

Just a couple suggestions.

TrevBart, 2023-03-16:
@feeneyai these are good suggestions. I have updated the readme with your notes. I have added a constant "bypassGPS" to allow the write out even without GPS data. Thanks!

Closed 2023-03-16.

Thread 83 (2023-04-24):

Payload building details

pankonen, 2023-04-24:
Add information on payload building:

- Antennas for trackers
- Camera mounting
- Batteries
- Payload mounting
- If found details on the box and in the box
- Other missing advice

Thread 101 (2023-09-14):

Question about separating senors

feeneyai, 2023-09-14:
One sensor we talked about adding was a display for checking to make sure all sensors are functioning as expected before the launch. I thought that could be a cool extension especially for AP CS A students that did this project last year in AP CS P.  I think I understood that can't be done with Arduinos because there is a memory issue on the Arduino board once all sensors are installed.  Would it be possible to split the sensors between 2 Arduinos and put displays on each board? I don't remember that they are necessarily tied to each other, but I guess they would be writing to the same SD card so maybe this could not work.

In our initial troubleshooting sessions, this could be a task some students "investigate" and report on after working with SF mentors that are intimately familiar with the payload, weights, power, etc.

If it can be done then maybe the payload for NCHS AP CS A could incorporate that and students could be involved with how to get that added to the payload so it is programmed to report the important data, visible, working correctly, etc. The whole class would not work on that but maybe one or two of the groups that have either programmed a lot or did the project in AP CS Principles. I have many sharp students but one in particular that was a SF intern and his group is pretty advanced.

Just a thought.

pankonen, 2023-09-14:
I'll add this to our agenda when the core team meats about extras in each lab. Thanks for the input.

We have memory limitations currently but ran out of time trying to get it going on the Arduino. It is in [lab 7](https://github.com/StateFarm-STEM/hablogger/tree/main/python/raspberrypico/lesson-7) for Pico's though. The memory limitations come in with all the sensors in place. If its just the display it would work fine likely.

Personally I'd like to see it in the beginning so we see the output from each lab on the display (as well as the serial monitor in the IDE), that would be pretty cool.

tdeknecht, 2023-10-26:
Thanks for the suggestion! It looks like Tom is on it.

For other suggestions and discussion related topics, please use the [Discussions](https://github.com/StateFarm-STEM/hablogger/discussions) feature in this project. We'll reserve the Issue board for features, enhancements, bugs, and other action items.

pankonen, 2023-10-26:
Amy we talked last night when we met and will work on a display for both the Arduino and pico for minimum the last lesson but possibly for others to show debug info. Stay tuned. I'll link the issue to solve this when I create it.

Closed 2023-10-26.

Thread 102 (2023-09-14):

Update code to allow the GPS to work at altitude

pankonen, 2023-09-14:
Remove altitude limitations we currently have with existing code.

@snarfattack and @ssamjung2 I think had an email trail with how to solve this. I tentatively assign them on this. We will discuss when we huddle as a core team as well.

tdeknecht, 2023-10-26:
Does this apply to both the `c` and `python` projects?

pankonen, 2023-12-06:
Honestly I'm not sure. I'm not sure I can easily identify which data files are Pico vs Arduino in the [folder](https://github.com/StateFarm-STEM/hablogger/tree/main/telemetry-analysis/flights). I THINK it was Android only.

I'll pop a story to update post flight procedures / tasks one being to upload the data to Github and identify the files a little better. I'll also make sure we are formatting the data the same and at the same time intervals.

snarfattack, 2023-12-19:
I copied code from the Arduino based APRS trackers that were working as expected at high altitude.
The GPS modules with GoouuuTech branding on them do not work when placed into high altitude mode. We get no lat/lon coordinates back from the module.
I purchased the [HiLetgo NEO-7M GPS](https://www.amazon.com/dp/B07X5GVW6Q) module instead, and the code works as expected at low altitude during testing. These modules have ublox branded gps chips.

Since we expect that classes will still use the old modules for now and we want them to still get locks and gps data at low altitude, I will upload the high altitude code to fly in a separate code file.

Closed 2023-12-28.

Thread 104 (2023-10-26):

Create fabricated GPS data for when GPS sensor does not connect

tdeknecht, 2023-10-26:
## Problem
Students will wire the GPS sensor. However, because students are in classrooms inside a building, the GPS sensor does not often receive information from satellites. This leads to an incomplete experience.

## Recommended Solution
Create fabricated data via a mock endpoint of sorts within the GPS plugin. The data should imitate what the real data would look like, allowing students to manipulate the data after wiring the device.

Closed 2024-02-07.

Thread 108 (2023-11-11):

Payload Development

kirksamp, 2023-11-11:
We got a look at the 3D printed box today in the classroom. It is likely that all of the schools this year have 3d printing capabilities. Is it too big of a jump to have the students design and print a box or print the box using the pattern currently in play?  Can they do more to design and build the payload structure and how components in the payload are secured?

pankonen, 2023-12-07:
I'll be walking through the current payloads Friday 12/8 and how we put them together. We will also spend the last session int eh classrooms doing the same with the students. As of now we use a foam cooler used to ship prescriptions through the mail. We have adapted [mounts](https://github.com/StateFarm-STEM/hablogger/tree/main/ballooninfo/3D%20Printed%20Camera%20Mounts) for the action cameras that sandwich the foam. We use duct tape or gaffing tape to mount items and to seal the payload that also doubles to help with visibility. They could most certainly print the camera holders as long as we can get them ahead of payload building. I've assigned Josh V (@snarfattack ) to add his thoughts.

I love the idea of this and have been wanting to print one ourselves but I'm not sure we are ready for it. We have many of variables to make sure we have successful flights if we can maybe my opinion can be changed:

- We would need to validate all things are met every payload at every school. I don't have the hours to do so right now. We already take 5-20 hours to prepare the coolers we fly now.
- We have been successful retrieving 2-3 payloads where the parachute failed. The foam coolers have been very successful absorbing the shock
- We would need to mount the cameras, battery packs, data loggers, radio components, antennas, and emergency contact information
- They would need to manage the extreme temperatures without:
  - Cracking / crumbling etc
  - Insulating the components for the duration of the flight as most of it cannot operate below -10c
  - Not fail from flight / structure stress in the cold temps
- UV stable

I'm sure I'm missing other thoughts...

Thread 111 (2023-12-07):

Lesson 3 - C - Add Challenge

pankonen, 2023-12-07:
Add a challenge to [lesson 3](https://github.com/StateFarm-STEM/hablogger/tree/main/c/arduino/lesson3) for groups that finish early or want to learn/explore more.

Some examples:
- Calculate altitude from pressure
- Calculate different temperature conversions (celsius, Fahrenheit, etc)
- Links to module docs, what else could they do with it

What to add:
- Explain the challenge
- Present some ideas
- Define what success looks like

tdeknecht, 2024-02-07:
Closed via https://github.com/StateFarm-STEM/hablogger/pull/142

Closed 2024-02-07.

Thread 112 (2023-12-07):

Lesson 4 - C - Add Challenge

pankonen, 2023-12-07:
Add a challenge to [lesson 4](https://github.com/StateFarm-STEM/hablogger/tree/main/c/arduino/lesson4) for groups that finish early or want to learn/explore more.

Some examples:
- Formatting output data better
- Number of satellites being received
- Add reference material for the GPS module or GPS infrastructure for additional research for students

What to add:
- Explain the challenge
- Present some ideas
- Define what success looks like

tdeknecht, 2024-02-07:
Closed via https://github.com/StateFarm-STEM/hablogger/pull/143

Closed 2024-02-07.

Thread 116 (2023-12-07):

Lesson 3 - Python - Add Challenge

pankonen, 2023-12-07:
Add a challenge to [lesson 3](https://github.com/StateFarm-STEM/hablogger/tree/main/python/raspberrypico/lesson-3) for groups that finish early or want to learn/explore more.

Some examples:
- Calculate altitude from pressure
- Calculate different temperature conversions (celsius, Fahrenheit, etc)
- Links to module docs, what else could they do with it

What to add:
- Explain the challenge
- Present some ideas
- Define what success looks like

tdeknecht, 2023-12-26:
Closed via https://github.com/StateFarm-STEM/hablogger/pull/132

Closed 2023-12-26.

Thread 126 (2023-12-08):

Arduino GPS lesson tx/rx issue

gregdirst, 2023-12-08:
Lesson 4 GPS lesson needs updated to match the GPS code and pin assignments as lesson 6.

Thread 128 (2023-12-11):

Pico Naming Consistency

jvanantwerp1, 2023-12-11:
Pin references change from hardware pin numbers to Pico GP pin numbers without consistency or warning.  This was very confusing to the teams.  My suggestion would be to use the Pico Pin References (VCC, GND, GP11, etc) because that matches to the provided diagram.

Mention could also be made of the hardware pin number.

tdeknecht, 2023-12-11:
Do you have an example of this?

I do see the table references both the physical pin and GPIO pin. Both are important because the physical pin is faster to reference when wiring, but the GPIO pin is crucial for the coding portion which is used to interface with the device plugged in to the physical pin.

We can make this clearer, but first need to learn where in the lesson(s) the confusion exists.

tdeknecht, 2023-12-18:
@pankonen Do we know how many Pico vs. Pico W's we have? One way around this is to go with the Pico only and standardize on it. It might also be cheaper from a hardware standpoint.

pankonen, 2023-12-18:
I don't know but would like to account for each as we have ordered this years already and I don't think I can add to the order. Normal Community purchased some of their own components to have smaller groups.

tdeknecht, 2023-12-26:
We'll need @jvanantwerp1 to weigh in and give more context to the original issue. However, @pankonen , there is an existing issue related to the Pico and Pico W disparity: https://github.com/StateFarm-STEM/hablogger/issues/124

I still suspect this issue is in reference to physical pin locations and GP pin assignments. To help with this, I've added clarity in Lesson 2 for the difference between these two: https://github.com/StateFarm-STEM/hablogger/tree/main/python/raspberrypico/lesson-2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

I will close this issue pending @jvanantwerp1 's response.

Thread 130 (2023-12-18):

Add notes in labs for validating pin layouts on components

pankonen, 2023-12-18:
Trevor and I are making some changes to the labs for consistency and based on this year’s huddle with mentors. We are updating images for some other things so we can call out where pins are labeled and the fact that it may be different always verify when wiring. We have this on some bit here and their so always better to have the attention to detail and documentation. I think we may have some differences here and there on random components and perhaps some Pico’s.

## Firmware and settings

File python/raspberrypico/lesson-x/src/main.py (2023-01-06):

from machine import Pin, SPI, I2C, UART
from drivers import sdcard
from drivers import gtu7 as gpsdriver
from drivers import bmp180 as bmp180driver
from ssd1306 import SSD1306_I2C

import os
import time
import _thread
    
    
def init_oled():
    # https://www.tomshardware.com/how-to/oled-display-raspberry-pi-pico
    i2c = I2C(0,
            sda=Pin(16),
            scl=Pin(17),
            freq = 400000)
    
    oled = SSD1306_I2C(128, 64, i2c) # width is 128, height is 64
    
    return oled


def init_bmp180(test=True):
    bus =  I2C(0,
               sda=Pin(16),
               scl=Pin(17),
               freq=100000)

    # Initialize BMP180 with previously defined I2C config
    bmp180 = bmp180driver.BMP180(bus)
    
    bmp180.oversample_sett = 2 # Accuracy, as defined in driver docs: https://github.com/micropython-IMU/micropython-bmp180
    bmp180.baseline = 101325   # Baseline pressure, as defined in driver docs: https://github.com/micropython-IMU/micropython-bmp180

    if test:
        try:
            assert isinstance(bmp180.temperature, float)
        except AssertionError:
            oled.text("BMP180_TEMP: ERR", 0, 0)
        else:
            oled.text("BMP180_TEMP: OK", 0, 0)

        try:
            assert isinstance(bmp180.pressure, float)
        except AssertionError:
            oled.text("BMP180_PRES: ERR", 0,10)
        else:
            oled.text("BMP180_PRES: OK", 0, 10)

        try:
            assert isinstance(bmp180.altitude, float)
        except AssertionError:
            oled.text("BMP180_ALTI: ERR", 0, 20)
        else:
            oled.text("BMP180_ALTI: OK", 0, 20)
            
        oled.show()

    return bmp180


def init_gtu7(test=True):
    uart = UART(1,
                baudrate=9600,
                timeout=3600,
                tx=Pin(4),
                rx=Pin(5))

    gtu7 = gpsdriver.GTU7(uart)
    
    if test:
        try:
            assert len(gtu7.gpgga()) == 4
        except AssertionError:
            oled.text("GTU7_GPGGA : ERR", 0, 30)
        else:
            oled.text("GTU7_GPGGA : OK", 0, 30)

        try:
            assert len(gtu7.gprmc()) == 5
        except AssertionError:
            oled.text("GTU7_GPRMC : ERR", 0,40)
        else:
            oled.text("GTU7_GPRMC : OK", 0, 40)
            
        oled.show()

    return gtu7


def init_sdcard(folder, test=True):
    spi = machine.SPI(1,
                      baudrate=1000000,     # 1 MHz
                      polarity=0,
                      phase=0,
                      bits=8,
                      firstbit=SPI.MSB,
                      sck=machine.Pin(10),  # Pico GPIO Pin 10
                      mosi=machine.Pin(11), # Pico GPIO Pin 11
                      miso=machine.Pin(12)) # Pico GPIO Pin 12
    sd = sdcard.SDCard(spi,Pin(13))
    
    os.mount(sd,folder)
    
    if test:
        try:
            assert folder[1:] in os.listdir()
        except AssertionError:
            oled.text("SD_CARD    : ERR", 0, 50)
        else:
            oled.text("SD_CARD    : OK", 0, 50)
            
        oled.show()


def write_csv_to_sdcard(folder, file_name, dataset, header=None):
    with open(folder + '/' + file_name,'a+') as csv_out:
        if header:
            dataset = header
            
        for data in dataset:
            if data == dataset[-1]:
                # If last element in the dataset, don't add a comma.
                csv_out.write('"'+str(data)+'"')
            else:
                csv_out.write('"'+str(data)+'",')
        csv_out.write('\n')


def read_csv_from_sdcard(folder, file_name):
    csv_data = []
    with open(folder + '/' + file_name,'r') as csv_in:
        for line in csv_in:
            line=line.rstrip('\n')
            line=line.rstrip('\r')
            csv_data.append(line.split(','))

    return csv_data


def delete_files_from_sdcard_folder(folder):
    for file in os.listdir(folder):
        try:
            os.remove(folder + '/' + file)
        except Exception as e:
            pass
            
            
if __name__ == "__main__":   
    led = Pin(25, Pin.OUT)  # Assign onboard LED to variable
    led.toggle()            # Toggle on the onboard LED
    
    oled = init_oled()      # Initialize the OLED display module
    
    try:
        sd_dir = '/sd'          # Directory created on SD card at root '/'. Expected format is '/<string>'. Example: '/sd'
        init_sdcard(sd_dir)     # Initialize the SD Card
        
        bmp180 = init_bmp180()  # Initialize the BMP_180 (Temp/Pressure module)
        gtu7 = init_gtu7()      # Initialize the GT-U7 (GPS module)

        delete_files_from_sdcard_folder('/sd') # Uncomment this to delete a folder and its contents.
        
        # Start a new thread and power off the OLED after a certain amount of time (in seconds)
        oled_off = lambda: (time.sleep(30), oled.poweroff())
        _thread.start_new_thread(oled_off, ())

        csv_header = [
            "date",
            "time",
            "latitude",
            "longitude",
            "velocity",
            "numSatellites",
            "temperature",
            "pressure",
            "altitude",
            ]
        write_csv_to_sdcard(sd_dir, "data.csv", None, csv_header) # Initialize CSV header
        
        for x in range(10):
            temp = bmp180.temperature  # Capture temperature, assign to `temp` variable
            p = bmp180.pressure        # Capture pressure, assign to `p` variable
            altitude = bmp180.altitude # Capture altitude, assign to `altitude` variable
            
            gpgga = gtu7.gpgga() # Capture NMEA GPGGA GPS data (http://aprs.gids.nl/nmea/#gga)
            gprmc = gtu7.gprmc() # Capture NMEA GPRMC GPS data (http://aprs.gids.nl/nmea/#rmc)
            
            data = [gprmc[0], gprmc[1], gprmc[2], gprmc[3], gprmc[4], gpgga[3], temp, p, altitude]
            
            write_csv_to_sdcard(sd_dir, "data.csv", data)
            
    except Exception as e:
        print(e)
        oled.fill(False)
        oled.text(str(e), 0, 0)
        oled.show()
        
    # Read all the rows from the CSV and print them to the console.
    #for row in read_csv_from_sdcard(sd_dir, "data.csv"):
    #    print(row)
    
    led.toggle() # Toggle off the onboard LED

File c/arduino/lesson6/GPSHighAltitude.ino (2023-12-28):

/*
  SD card datalogger

  This example shows how to log data from three analog sensors
  to an SD card using the SD library.

  The circuit:
   analog sensors on analog ins 0, 1, and 2
   SD card attached to SPI bus as follows:
 ** MOSI - pin 11
 ** MISO - pin 12
 ** CLK - pin 13
 ** CS - pin 10 (for MKRZero SD: SDCARD_SS_PIN)

  created  24 Nov 2010
  modified 9 Apr 2012
  by Tom Igoe

  This example code is in the public domain.

*/

#include <SPI.h>
#include <SD.h>
#include "Adafruit_BMP085.h"
#include <TinyGPS++.h>
#include <SoftwareSerial.h>

const int chipSelect = 10;
const bool bypassGPS = true;

static const int RXPin = 4, TXPin = 3;
static const uint32_t GPSBaud = 9600;
TinyGPSPlus gps;

// map software serial to gps
SoftwareSerial serialgps(TXPin, RXPin);

Adafruit_BMP085 bmp;

void setup() {
  // Open serial communications and wait for port to open:
  Serial.begin(9600);
  delay(1000);


  Serial.print("initializing sd card...");

  // see if the card is present and can be initialized:
  if (!SD.begin(chipSelect)) {
    Serial.println("SD Init Failed");
    // don't do anything more:
    while (1);
  }
  Serial.println("Initialized");
  // see if the card is present and can be initialized:
  if (!SD.begin(chipSelect)) {
    Serial.println("failed");
    // don't do anything more:
    while (1);
  }
  Serial.println("initialized");

  initBMP();
  initGPS();
}


void loop() {
  
  // make a string for assembling the data to log:
  String dataString = "";
  bool gpsready = false;

  unsigned long start = millis();
  do
  {
    while (serialgps.available()>0) {
      char c;
      c=serialgps.read();
      gps.encode(c);
    }
  } while (millis() - start < 5000);

  float c = bmp.readTemperature();  // Variable for holding temp in C
  float f = c*1.8 + 32.;  // Variable for holding temp in F
  // //float pressure = bmp.readPressure()/3386.3887; //pascals to in of mercury
  float p = bmp.readPressure(); //pascals
  
  dataString += String(c, 2);
  dataString += ",";
  dataString += String(f, 2);
  dataString += ",";
  dataString += String(p, 2);
  dataString += ",";
  
  if ((gps.location.age() < 1000 || gps.location.isUpdated()) && gps.location.isValid()) {
    if (gps.satellites.isValid() && (gps.satellites.value() > 3)) {
      dataString += (gps.course.isValid() ? (int)gps.course.deg() : 0);
      dataString += ",";
      dataString += (gps.speed.isValid() ? (int)gps.speed.knots() : 0);
      dataString += ",";
      dataString += (gps.location.isValid() ? (long)gps.altitude.feet() : 0);
      dataString += ",";
      dataString += (gps.hdop.isValid() ? (int)gps.hdop.value() : 0);
      dataString += ",";
      dataString += (gps.satellites.isValid() ? (int)gps.satellites.value() : 0);
      dataString += ",";
      dataString += (gps.location.isValid() ? (int)gps.location.age() : 0);
    
      float lat = gps.location.isValid() ? gps.location.lat() : 0;
      float lng = gps.location.isValid() ? gps.location.lng() : 0;
      
      dataString += ",";
      dataString += String(lat, 6);
      dataString += ",";
      dataString += String(lng, 6);
      dataString += ",";
      dataString += gps.charsProcessed();
      dataString += ",";
      dataString += gps.failedChecksum();
      dataString += ",";

      if (gps.date.isValid())
      {
        if (gps.date.month() < 10) dataString += String(F("0"));
        dataString += String(gps.date.month());
        dataString += String(F("/"));
        if (gps.date.day() < 10) dataString += String(F("0"));
        dataString += String(gps.date.day());
        dataString += String(F("/"));
        if (gps.date.year() < 10) dataString += String(F("0"));
        dataString += String(gps.date.year());
      }
      else
        dataString += "00/00/00";

      dataString += String(F(","));
  
      if (gps.time.isValid())
      {
        if (gps.time.hour() < 10) dataString += String(F("0"));
        dataString += String(gps.time.hour());
        dataString += String(F(":"));
        if (gps.time.minute() < 10) dataString += String(F("0"));
        dataString += String(gps.time.minute());
        dataString += String(F(":"));
        if (gps.time.second() < 10) dataString += String(F("0"));
        dataString += String(gps.time.second());
        dataString += String(F("."));
        dataString += String(gps.time.centisecond());
      }

      gpsready = true;
    }
  }

  if (gpsready || bypassGPS) {
    // open the file. note that only one file can be open at a time,
    // so you have to close this one before opening another.
    //File dataFile = SD.open("datalog.txt", FILE_WRITE);
  
    // if the file is available, write to it:
    // if (dataFile) {
    //   dataFile.println(dataString);
    //   //dataFile.close();
    //   dataFile.flush();

    // }
    // if the file isn't open, pop up an error:
    // else {
    //   Serial.println("error opening datalog.txt");
    // }
    // print to the serial port too:
    Serial.println(dataString);
  }

  delay(2000);
}

void initGPS(){
  Serial.print("\ninitializing gps...");
  
  serialgps.begin(GPSBaud);
  delay(2000);
  if (!serialgps.available()) {
    Serial.println("GPS initialization failed");
    while (1);
  }
  else {
    resetGPS();
    setGPS_DynamicMode6();

    Serial.println("GPS initialized");
  }
}

void initBMP(){
  Serial.print("\ninitializing bmp180...");

  unsigned status;
  
  status = bmp.begin();
  if (!status) {
    Serial.println("failed");
  }
  else {
    Serial.println("bmp initialized");
  }
}

void sendUBX(uint8_t *MSG, uint8_t len) {
  serialgps.flush();
  serialgps.write(0xFF);
  wait(100);
  for(int i=0; i<len; i++) {
    serialgps.write(MSG[i]);
  }
}

boolean getUBX_ACK(uint8_t *MSG) {
  uint8_t b;
  uint8_t ackByteID = 0;
  uint8_t ackPacket[10];
  unsigned long startTime = millis();

  // Construct the expected ACK packet    
  ackPacket[0] = 0xB5;	// header
  ackPacket[1] = 0x62;	// header
  ackPacket[2] = 0x05;	// class
  ackPacket[3] = 0x01;	// id
  ackPacket[4] = 0x02;	// length
  ackPacket[5] = 0x00;
  ackPacket[6] = MSG[2];	// ACK class
  ackPacket[7] = MSG[3];	// ACK id
  ackPacket[8] = 0;		// CK_A
  ackPacket[9] = 0;		// CK_B

  // Calculate the checksums
  for (uint8_t ubxi=2; ubxi<8; ubxi++) {
    ackPacket[8] = ackPacket[8] + ackPacket[ubxi];
    ackPacket[9] = ackPacket[9] + ackPacket[8];
  }

  while (1) {

    // Test for success
    if (ackByteID > 9) {
      // All packets in order!
      return true;
    }

    // Timeout if no valid response in 3 seconds
    if (millis() - startTime > 3000) { 
      return false;
    }

    // Make sure data is available to read
    if (serialgps.available()) {
      b = serialgps.read();

      // Check that bytes arrive in sequence as per expected ACK packet
      if (b == ackPacket[ackByteID]) { 
        ackByteID++;
      } 
      else {
        ackByteID = 0;	// Reset and look again, invalid order
      }

    }
  }
}
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

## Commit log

2022-10-12 pico hardware updates
    pico hardware updates
2022-10-19 Updated arduino lessons from old archive
    Updated arduino lessons from old archive
2022-10-29 Uploading LED blink .py files
2022-11-17 refactor: adjusted code; added driver
2022-11-20 refactor: changing lesson 4 to include a driver
2022-11-20 fix: returning proper data types
    [gtu7.py]
2022-11-22 fix: bug in driver. cleaned up example code
    [gtu7.py, main.py]
2022-11-22 feat: brought in the updated gps driver and added logic to write its data to sd card
2022-12-01 Create 3D Printed Camera Mounts
2022-12-10 docs: updated to reflect new steps for drivers
2022-12-10 docs: moved drivers to drivers folder
2022-12-10 refactor: simplified LED code; doc update to reflect driver change
2022-12-10 refactor: reorganized order to make it easier to compare to driver order
2023-01-01 Delete c/raspberrypico directory
    Directory moved to different location...cleaning up
2023-01-02 full wired picutre
2023-01-31 Arduino workbench based on frog box
    [Frog Box Lid thin.stl, Frog Box no Seal - Part 1.stl, hinge_looser.stl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]
2023-02-03 Start of addition for three LEDs
2023-02-03 Lesson 1 - c
    updated lesson 1 under c / arduino
2023-02-03 New video with multiple LEDs
2023-02-03 Added web version of arduino studio
    Added web version of arduino studio
2023-02-17 File extension case
    There is an issue with the PNG file extension case causing the image to not load.
2023-02-19 Pico workbench, license + readme for arduino
    [Frog Box Lid Pico Screw.stl, Frog Box no Seal.stl, hinge_looser.stl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]
2023-03-01 Wire up image
2023-03-01 Pin out update
2023-03-03 LED pin change
    Change to Pico pin for LED and add comment changes for PicoW.
2023-03-03 refactor: removing LED entirely
2023-03-03 fix: corrected a comment
    [main.py]
2023-03-03 fix: adding back lib. accidentally removed
    [main.py]
2023-03-03 fix: removed LED logic
    [main.py]
2023-03-03 feat: adding clearer logic and print statements
2023-03-08 Update README.md
    Swap wiring diagram for pins 10 and 11, they were backwards
2023-03-09 Updates for main second mount and final output picture
2023-03-09 Added wire up image
2023-03-09 Arduino wireup and thought starters. Pico video!
2023-03-13 fix: addressing some concerns in issue 67
    [main.py]
2023-03-15 Moving workbench files
    - Moved Pico workbench 3d print info to the Python directory for now.
    - Moved the Arduino workbench to the C/Arduino directory for now
    [Frog Box Lid Pico Screw.stl, Frog Box Lid thin.stl, Frog Box no Seal - Part 1.stl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]
2023-03-16 Lesson six Arduino updates.
2023-03-16 Double mount for some SD cards
    I had issues with some SD cards not mounting correctly. A simple fix I found was to catch the error and just mount again.
    [main.py]
2023-04-19 STL adds
    Adding additional 3d print STL's for camera mounts
    [NEWCAMMOUNT.stl, NEWCAMMOUNTv2.stl, NEWCAMMOUNTv3.stl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]
2023-04-23 Added a new design to hold cameras
    [Akaso Mount Back.stl, Akaso Mount.stl]
2023-04-26 Updated items needed for the launch
    - Added items used to prepare, track, and launch the balloons
2023-04-26 Added data
    - Added data from 7-21-2023 Normal West flights
    [data.csv]
2023-05-01 Swap data and corrected date
    [data.csv]
2023-05-01 Adding data logger files
    Adding data logger files from Pi Pico and Arduino
    [data.csv]
2023-05-09 Add files via upload
    Adding powerpoint
2023-08-20 Arduino lid that uses screws to hold breadboard
    [Frog Box Lid Screws.stl]
2023-11-10 Update november.md
    Added temperature issues
2023-12-08 Update README.md
    Suggesting a couple of updates to make the driver download, store, and pull instructions a little more clear.
2023-12-17 docs: added challenge to lesson 2 related to issue 115
    [main.py]
2023-12-18 Moving antenna models to amateur radio
2023-12-18 adding APRS telemetry data
    [International Standard Atmosphere Table.xlsx, KB9LNS-13.xlsx, KB9LNS-14.xlsx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]
2023-12-21 fix: accidentally override source with challenge. Corrected
    [main.py]
2023-12-21 docs: added more troubleshooting hints for LED
2023-12-27 Arduino support for GPS mode 6
2024-02-07 feat: added fake endpoint option for gpgga and gprmc data for issue 104
    [gtu7.py]
2024-02-07 feat: adding missing code
    [gtu7.py]
2024-02-23 fix: wiring diagram had backwards wiring
2024-03-12 fix: corrected wiring for SD card
2024-03-15 Payload presentation
    Powerpoint for payload presentation in classrooms
2024-03-22 fix: added OLED driver for workaround in case school firewall blocks package downloads
